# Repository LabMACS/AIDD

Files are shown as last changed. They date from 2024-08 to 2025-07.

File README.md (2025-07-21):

# A.I.D.D.
The Artificial Intelligent Dolphin Deterrent: a novel low-cost intelligent robotic system capable of identifying dolphin vocalizations and consequently responding in real-time to dissuade the dolphins from approaching.

<p float="left">
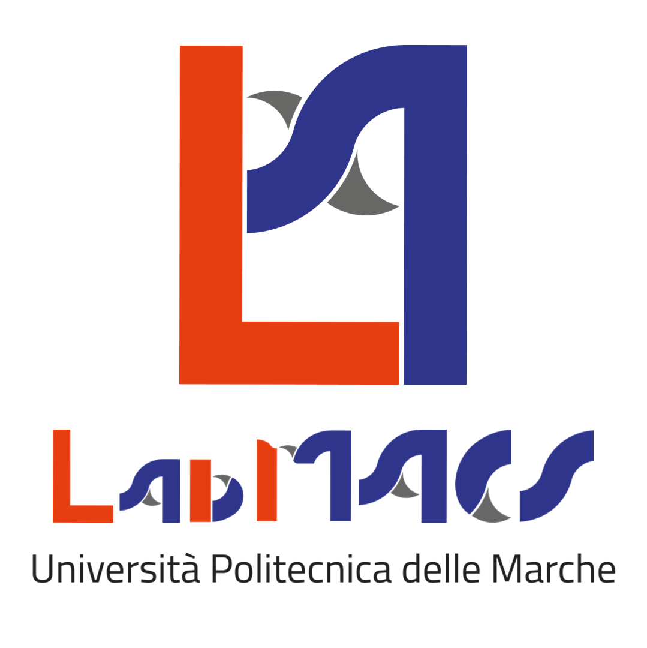
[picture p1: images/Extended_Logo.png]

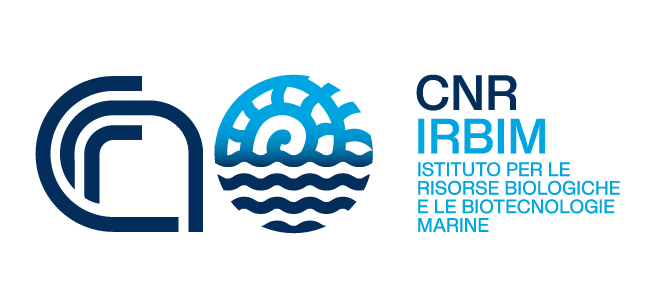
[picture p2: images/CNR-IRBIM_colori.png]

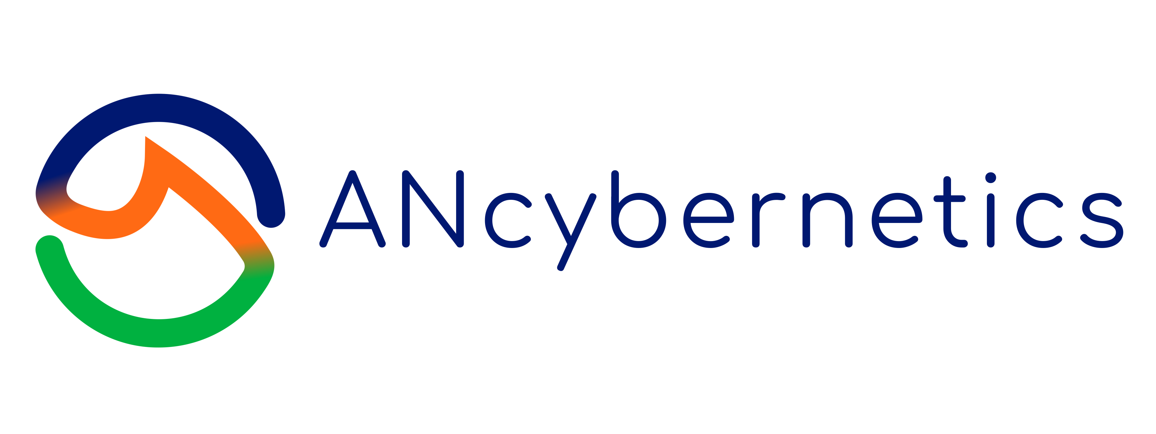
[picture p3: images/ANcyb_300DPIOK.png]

</p>

# Table of contents
1. [Preface](#preface)
2. [Legal](#legal)
    1. [Credits](#credits)
    2. [Funding](#funding) 
    3. [License](#license)

## Preface 
Dolphin bycatch and depredation in commercial fisheries pose serious ecological and socio-economic challenges, often resulting in injury or death of non-target marine mammals and financial loss for fishers. Conventional mitigation strategies, including static acoustic deterrent devices (pingers), have shown limited long-term efficacy due to habituation, non-selective operation, and environmental side effects. In this repository, we introduce the Artificial Intelligent Dolphin Deterrent (A.I.D.D.), a novel low-cost mechatronic system designed to reduce dolphin bycatch through underwater acoustic sensing, real-time machine learning, and programmable deterrent emissions.The device features a hydrophone-based acquisition unit, a Raspberry Pi Zero 2 W for onboard processing, and a dual-function acquisition/emitter system powered by a customized preamplifier and amplifier chain. The computational core of the system is a convolutional neural network (CNN) optimized with TensorFlow Lite to detect dolphin whistles and trigger deterrent sounds only upon verified presence
This repository provides:

    The complete Electronic Scheme of A.I.D.D.

    An advanced version of the convolutional neural network (CNN) optimized with TensorFlow Lite

    The Electronic scheme of the Power Monitoring module and its calculation software

    STL files for 3D printing the hydrophone

A.I.D.D. is a low-cost, fully replicable, and customizable solution that aims to make intelligent bycatch mitigation technologies accessible, representing a promising step toward sustainable and intelligent fishery practices.
  
***
For further information about the project and the A.I.D.D., please look at 
- https://www.irbim.cnr.it/progetto-dettagli/life-delfi/
- Francesco Di Nardo,  Rocco De Marco, Daniele Costa, Alessandro Lucchetti, and David Scaradozzi. A.I.D.D.: A Low-Cost, AI Powered, Acoustic Deterrent to Prevent Dolphin Bycatch and Depredation, Submitted to Science Robotics, July 2025.
- Rocco De Marco, Francesco Di Nardo, Alessandro Rongoni, Laura Screpanti, and David Scaradozzi. Real-Time Dolphin Whistle Detection on Raspberry Pi Zero 2 W with a TFLite Convolutional Neural Network. Robotics 2025, 14, 67. https://doi.org/10.3390/robotics14050067
- David Scaradozzi, Rocco de Marco, Daniel Li Veli, Alessandro Lucchetti, Laura Screpanti, and Francesco Di Nardo, Convolutional Neural Networks for Enhancing Detection of Dolphin Whistles in a Dense Acoustic Environment. IEEE Access, 2024, 12, 127141-127148.  doi: 10.1109/ACCESS.2024.3454815
- Rocco De Marco, Francesco Di Nardo, Alessandro Lucchetti, Massimo Virgili, Andrea Petetta, Daniel Li Veli, Laura Screpanti, Veronica Bartolucci, David Scaradozzi. The Development of a Low-Cost Hydrophone for Passive Acoustic Monitoring of Dolphin’s Vocalizations. Remote Sensing. 2023, 15, 1946. https://doi.org/10.3390/rs15071946
***

## Legal 
### Credits 
If you have any suggestions or comments related to this software, please contact:
* **Project Leader**: [David Scaradozzi](mailto:d.scaradozzi@univpm.it)
* **Project Developer**: [Rocco De Marco](mailto:rocco.demarco@cnr.it)
* **Project Developer**: [Francesco Di Nardo](mailto:f.dinardo@univpm.it)

- *LabMACS, DII, UniversitÃ  Politecnica delle Marche, Via Brecce Bianche, 12, Ancona, 60131, Italy*
- *Institute of Biological Resources and Marine Biotechnology (IRBIM), National Research Council (CNR), Ancona, Italy.*
- *ANcybernetics, Università Politecnica delle Marche, Ancona, Italy.*

[https://www.labmacs.university/](https://www.labmacs.university/)

### Funding  
This work was supported in part by LIFE Financial Instrument of the European Community, Life Delfi Project – Dolphin Experience: Lowering Fishing Interactions (LIFE18NAT/IT/000942) and by the National Recovery and Resilience Plan (NRRP), Mission 4 Component 2 Investment 1.4 (Call for tender No. 3138 of 16 December 2021, rectified by Decree n.3175 of 18 December 2021 of Italian Ministry of University and Research funded by the European Union) NextGenerationEU.

### License 
[][cc-by-nc-sa]

This work is licensed under a
[Creative Commons Attribution-NonCommercial-ShareAlike 4.0 International License][cc-by-nc-sa].

[][cc-by-nc-sa]

[cc-by-nc-sa]: http://creativecommons.org/licenses/by-nc-sa/4.0/
[cc-by-nc-sa-image]: https://licensebuttons.net/l/by-nc-sa/4.0/88x31.png
[cc-by-nc-sa-shield]: https://img.shields.io/badge/License-CC%20BY--NC--SA%204.0-lightgrey.svg

To acknowledge the material, the following information must be reported:
* Attribution: DELFI project
             <[https://www.labmacs.university/](https://www.labmacs.university/)> 
* Title of the Work: AIDD - AI Dolphin Deter 
* Source: [https://github.com/LabMACS/AIDD](https://github.com/LabMACS/AIDD)
* License information: CC BY-NC-SA 4.0

The AIDD - AI Dolphin Deter is free available.

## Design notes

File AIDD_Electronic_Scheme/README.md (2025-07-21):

# A.I.D.D. Electronic schemes
The electronic schemes developed for A.I.D.D.

<p float="left">



</p>

# Table of contents
1. [Preface](#preface)
2. [Legal](#legal)
    1. [Credits](#credits)
    2. [Funding](#funding) 
    3. [License](#license)

## Preface 
This section contains the electronic schemes developed for A.I.D.D.. The "main board" fold includes the schematics, PCB, and Gerber files of the main device, which connects each specialised module composing the A.I.D.D.. This board presents two 40-pins socket connector to mount the Raspberry Pi Zero 2 W and the high-quality audio expansion board, the HiFiBerry DAC+ADC Pro. The board allows to connect the customized preamplifier ("PreAmp THT" fold). The signal preamplifier is composed of Microchip MCP6024 quad operational amplifier, with a constant gain-bandwidth product (10 MHz). It works with a single supply voltage range of 2.5 - 5.5 V. Further pre-assembled modules are pluggeble on the main board, such as the TDA2030A power amp, Step-Up DC-DC Converter, Relay modules and Real-Time Clock module. Further information could be found in the scientific article under submission.

***
For further information about the project, model and parameters, please look at 
- https://www.irbim.cnr.it/progetto-dettagli/life-delfi/
-Francesco Di Nardo, Rocco De Marco, Daniele Costa, Alessandro Lucchetti, and David Scaradozzi. A.I.D.D.: A Low-Cost, AI Powered, Acoustic Deterrent to Prevent Dolphin Bycatch and Depredation, Submitted to Science Robotics, July 2025.
***

## Legal 
### Credits 
If you have any suggestions or comments related to this software, please contact:
* **Project Leader**: [David Scaradozzi](mailto:d.scaradozzi@univpm.it)
* **Project Developer**: [Rocco De Marco](mailto:rocco.demarco@cnr.it)
* **Project Developer**: [Francesco Di Nardo](mailto:f.dinardo@univpm.it)

- *LabMACS, DII, UniversitÃ  Politecnica delle Marche, Via Brecce Bianche, 12, Ancona, 60131, Italy*
- *Institute of Biological Resources and Marine Biotechnology (IRBIM), National Research Council (CNR), Ancona, Italy.*
- *ANcybernetics, Università Politecnica delle Marche, Ancona, Italy.*

[https://www.labmacs.university/](https://www.labmacs.university/)

### Funding  
This work was supported in part by LIFE Financial Instrument of the European Community, Life Delfi Project – Dolphin Experience: Lowering Fishing Interactions (LIFE18NAT/IT/000942) and by the National Recovery and Resilience Plan (NRRP), Mission 4 Component 2 Investment 1.4 (Call for tender No. 3138 of 16 December 2021, rectified by Decree n.3175 of 18 December 2021 of Italian Ministry of University and Research funded by the European Union) NextGenerationEU.

### License 
[][cc-by-nc-sa]

This work is licensed under a
[Creative Commons Attribution-NonCommercial-ShareAlike 4.0 International License][cc-by-nc-sa].

[][cc-by-nc-sa]

[cc-by-nc-sa]: http://creativecommons.org/licenses/by-nc-sa/4.0/
[cc-by-nc-sa-image]: https://licensebuttons.net/l/by-nc-sa/4.0/88x31.png
[cc-by-nc-sa-shield]: https://img.shields.io/badge/License-CC%20BY--NC--SA%204.0-lightgrey.svg

To acknowledge the material, the following information must be reported:
* Attribution: DELFI project
             <[https://www.labmacs.university/](https://www.labmacs.university/)> 
* Title of the Work: AIDD - AI Dolphin Deter 
* Source: [https://github.com/LabMACS/AIDD](https://github.com/LabMACS/AIDD)
* License information: CC BY-NC-SA 4.0

The AIDD - AI Dolphin Deter is free available.

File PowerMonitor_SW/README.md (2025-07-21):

# Monitoring of Power Consumption
Software for the monitoring of A.I.D.D. power consumption.

<p float="left">



</p>

# Table of contents
1. [Preface](#preface)
2. [Legal](#legal)
    1. [Credits](#credits)
    2. [Funding](#funding) 
    3. [License](#license)

## Preface 
The enclosed routine (INA_219_Logger) is designed to provide an estimation of the power consumption of the A.I.D.D. device using a 12-bit I2C output digital power monitor, the INA219 sensor. The sensor was connected to a monitoring system based on a Raspberry Pi 3 Model A running Python sampling software. This setup acquires the voltage and current supplied to the A.I.D.D. system and classifies seven different operating stages: 

1.	Data read from audio device 
2.	STFT process
3.	Image conversion (Plot)
4.	CNN inference
5.	Data logging (in case of positive events)
6.	Sleep mode (waiting for the timestep of 0.4s)
7.	Start-up of the environment

The running states were transmitted from the Raspberry Pi Zero 2 W of the device to the monitoring Raspberry Pi 3 Model A via a three-wire GPIO connection (using GPIO pins 27, 17, and 22). These pins encoded the current running stage as a 3-bit integer value. The trials were conducted using the same criteria as in the previous section (Real-time software validation). 

***
For further information about the project, model and parameters, please look at 
- https://www.irbim.cnr.it/progetto-dettagli/life-delfi/
- Francesco Di Nardo, David Scaradozzi, Rocco De Marco, Laura Screpanti, and Alessandro Lucchetti, Intelligent identification of dolphin whistle in acoustic signals via convolutional neural networks, Science Advances, Submitted
***

## Legal 
### Credits 
If you have any suggestions or comments related to this software, please contact:
* **Project Leader**: [David Scaradozzi](mailto:d.scaradozzi@univpm.it)
* **Project Developer**: [Rocco De Marco](mailto:rocco.demarco@cnr.it)
* **Project Developer**: [Francesco Di Nardo](mailto:f.dinardo@univpm.it)

- *LabMACS, DII, UniversitÃ  Politecnica delle Marche, Via Brecce Bianche, 12, Ancona, 60131, Italy*
- *Institute of Biological Resources and Marine Biotechnology (IRBIM), National Research Council (CNR), Ancona, Italy.*
- *ANcybernetics, Università Politecnica delle Marche, Ancona, Italy.*

[https://www.labmacs.university/](https://www.labmacs.university/)

### Funding  
This work was supported in part by LIFE Financial Instrument of the European Community, Life Delfi Project – Dolphin Experience: Lowering Fishing Interactions (LIFE18NAT/IT/000942) and by the National Recovery and Resilience Plan (NRRP), Mission 4 Component 2 Investment 1.4 (Call for tender No. 3138 of 16 December 2021, rectified by Decree n.3175 of 18 December 2021 of Italian Ministry of University and Research funded by the European Union) NextGenerationEU.

### License 
[][cc-by-nc-sa]

This work is licensed under a
[Creative Commons Attribution-NonCommercial-ShareAlike 4.0 International License][cc-by-nc-sa].

[][cc-by-nc-sa]

[cc-by-nc-sa]: http://creativecommons.org/licenses/by-nc-sa/4.0/
[cc-by-nc-sa-image]: https://licensebuttons.net/l/by-nc-sa/4.0/88x31.png
[cc-by-nc-sa-shield]: https://img.shields.io/badge/License-CC%20BY--NC--SA%204.0-lightgrey.svg

To acknowledge the material, the following information must be reported:
* Attribution: DELFI project
             <[https://www.labmacs.university/](https://www.labmacs.university/)> 
* Title of the Work: AIDD - AI Dolphin Deter 
* Source: [https://github.com/LabMACS/AIDD](https://github.com/LabMACS/AIDD)
* License information: CC BY-NC-SA 4.0

The AIDD - AI Dolphin Deter is free available.

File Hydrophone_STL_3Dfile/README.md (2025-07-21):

# Hydrophone STL 3Dfile
The model files for 3D print of self-made CoPiDi hydrophone

<p float="left">



</p>

# Table of contents
1. [Preface](#preface)
2. [Legal](#legal)
    1. [Credits](#credits)
    2. [Funding](#funding) 
    3. [License](#license)

## Preface 
This section shares the STL files for the specific-developed enclosure cap that embeds the hydrophone/emitter device, based on piezo caps. This cap is designed to hermetically seal a 40cm-long Teflon tube that contains the device hardware in order to ensure watertightness. This component was made using an industrial-quality SLA (stereolithography) 3D printer, reproducing the already validated CoPiDi* hydrophone, with same form and dimensions. The cap can be removed to access the hydrophone and other components without compromising the waterproofing.  
***

Further details about CoPiDi hydrophone could be found in "De Marco, R.; Di Nardo, F.; Lucchetti, A.; Virgili, M.; Petetta, A.; Li Veli, D.; Screpanti, L.; Rocco De Marco, Francesco Di Nardo, Alessandro Lucchetti, Massimo Virgili, Andrea Petetta, Daniel Li Veli, Laura Screpanti, Veronica Bartolucci, David Scaradozzi. The Development of a Low-Cost Hydrophone for Passive Acoustic Monitoring of Dolphin’s Vocalizations. Remote Sensing. 2023, 15, 1946. https://doi.org/10.3390/rs15071946

For further information about the project, model and parameters, please look at 
- https://www.irbim.cnr.it/progetto-dettagli/life-delfi/
***

## Legal 
### Credits 
If you have any suggestions or comments related to this software, please contact:
* **Project Leader**: [David Scaradozzi](mailto:d.scaradozzi@univpm.it)
* **Project Developer**: [Rocco De Marco](mailto:rocco.demarco@cnr.it)
* **Project Developer**: [Francesco Di Nardo](mailto:f.dinardo@univpm.it)

- *LabMACS, DII, UniversitÃ  Politecnica delle Marche, Via Brecce Bianche, 12, Ancona, 60131, Italy*
- *Institute of Biological Resources and Marine Biotechnology (IRBIM), National Research Council (CNR), Ancona, Italy.*
- *ANcybernetics, Università Politecnica delle Marche, Ancona, Italy.*

[https://www.labmacs.university/](https://www.labmacs.university/)

### Funding  
This work was supported in part by LIFE Financial Instrument of the European Community, Life Delfi Project – Dolphin Experience: Lowering Fishing Interactions (LIFE18NAT/IT/000942) and by the National Recovery and Resilience Plan (NRRP), Mission 4 Component 2 Investment 1.4 (Call for tender No. 3138 of 16 December 2021, rectified by Decree n.3175 of 18 December 2021 of Italian Ministry of University and Research funded by the European Union) NextGenerationEU.

### License 
[][cc-by-nc-sa]

This work is licensed under a
[Creative Commons Attribution-NonCommercial-ShareAlike 4.0 International License][cc-by-nc-sa].

[][cc-by-nc-sa]

[cc-by-nc-sa]: http://creativecommons.org/licenses/by-nc-sa/4.0/
[cc-by-nc-sa-image]: https://licensebuttons.net/l/by-nc-sa/4.0/88x31.png
[cc-by-nc-sa-shield]: https://img.shields.io/badge/License-CC%20BY--NC--SA%204.0-lightgrey.svg

To acknowledge the material, the following information must be reported:
* Attribution: DELFI project
             <[https://www.labmacs.university/](https://www.labmacs.university/)> 
* Title of the Work: AIDD - AI Dolphin Deter 
* Source: [https://github.com/LabMACS/AIDD](https://github.com/LabMACS/AIDD)
* License information: CC BY-NC-SA 4.0

The AIDD - AI Dolphin Deter is free available.

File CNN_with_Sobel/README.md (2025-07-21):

# CNN trained with Sobel-filtered spectrograms
This section of the A.I.D.D. repository introduces the basic algorithm to test the functionality of the CNN model trained to recognize bottlenose dolphin whistles.

<p float="left">



</p>

# Table of contents
1. [Preface](#preface)
2. [Installation](#installation)
    1. [Requirements](#requirements)
    2. [Usage](#run)
3. [Legal](#legal)
    1. [Credits](#credits)
    2. [Funding](#funding) 
    3. [License](#license)

## Preface 
This section of the A.I.D.D. repository provides the convolutional neural network (CNN) that forms the computational core of the device, designed to identify dolphin whistles from spectrograms extracted from underwater audio recordings. Prior to CNN processing, spectrograms undergo a vertical Sobel filter that enhances the whistle waveform, improving both CNN training and detection performance. Two distinct datasets of dolphin vocalizations were used to evaluate CNN performance, with results showing that, in the best-case scenario, nearly all whistles were correctly identified (99.8%), and the mean model accuracy, precision, recall, and F1-score never dropped below 99.0%. Model effectiveness remained high even under challenging conditions with overlapping noise or other vocalizations. Moreover, the computation speed is fully compatible with real-time applications. The robustness of this model across environments and its low computational demand make this approach highly suitable for intelligent robotic solutions aimed at monitoring and mitigating underwater interactions.

The neural network presented here is an evolution of the one introduced in:

D. Scaradozzi, R. de Marco, D. Li Veli, A. Lucchetti, L. Screpanti, and F. Di Nardo, 'Convolutional Neural Networks for Enhancing Detection of Dolphin Whistles in a Dense Acoustic Environment,' in IEEE Access, vol. 12, pp. 127141-127148, 2024, doi: 10.1109/ACCESS.2024.3454815

which was originally used as the computational core of the device

***
For further information about the project, model and parameters, please look at 
- https://www.irbim.cnr.it/progetto-dettagli/life-delfi/
-  David Scaradozzi, Rocco De Marco, Laura Screpanti, and Francesco Di Nardo, Intelligent Identification of Dolphin Whistle in Acoustic Signals via Deep Learning, Scientific Reports, Submitted
***

## Installation 
### Requirements 
* TbD 
  
### Usage 
This simple application requires that spectrograms be prepared by applying a Sobel vertical filter and saved in PNG format with a resolution of 300x150 pixels. Files containing whistles should have filenames starting with POS, otherwise NEG. All these files should be saved in a folder named "sobel". Please note: a sample trained model is available in "Release"

## Legal 
### Credits 
If you have any suggestions or comments related to this software, please contact:
* **Project Leader**: [David Scaradozzi](mailto:d.scaradozzi@univpm.it)
* **Project Developer**: [Rocco De Marco](mailto:rocco.demarco@cnr.it)
* **Project Developer**: [Francesco Di Nardo](mailto:f.dinardo@univpm.it)

- *LabMACS, DII, UniversitÃ  Politecnica delle Marche, Via Brecce Bianche, 12, Ancona, 60131, Italy*
- *Institute of Biological Resources and Marine Biotechnology (IRBIM), National Research Council (CNR), Ancona, Italy.*
- *ANcybernetics, Università Politecnica delle Marche, Ancona, Italy.*

[https://www.labmacs.university/](https://www.labmacs.university/)

### Funding  
This work was supported in part by LIFE Financial Instrument of the European Community, Life Delfi Project – Dolphin Experience: Lowering Fishing Interactions (LIFE18NAT/IT/000942) and by the National Recovery and Resilience Plan (NRRP), Mission 4 Component 2 Investment 1.4 (Call for tender No. 3138 of 16 December 2021, rectified by Decree n.3175 of 18 December 2021 of Italian Ministry of University and Research funded by the European Union) NextGenerationEU.

### License 
[][cc-by-nc-sa]

This work is licensed under a
[Creative Commons Attribution-NonCommercial-ShareAlike 4.0 International License][cc-by-nc-sa].

[][cc-by-nc-sa]

[cc-by-nc-sa]: http://creativecommons.org/licenses/by-nc-sa/4.0/
[cc-by-nc-sa-image]: https://licensebuttons.net/l/by-nc-sa/4.0/88x31.png
[cc-by-nc-sa-shield]: https://img.shields.io/badge/License-CC%20BY--NC--SA%204.0-lightgrey.svg

To acknowledge the material, the following information must be reported:
* Attribution: DELFI project
             <[https://www.labmacs.university/](https://www.labmacs.university/)> 
* Title of the Work: AIDD - AI Dolphin Deter 
* Source: [https://github.com/LabMACS/AIDD](https://github.com/LabMACS/AIDD)
* License information: CC BY-NC-SA 4.0

The AIDD - AI Dolphin Deter is free available.

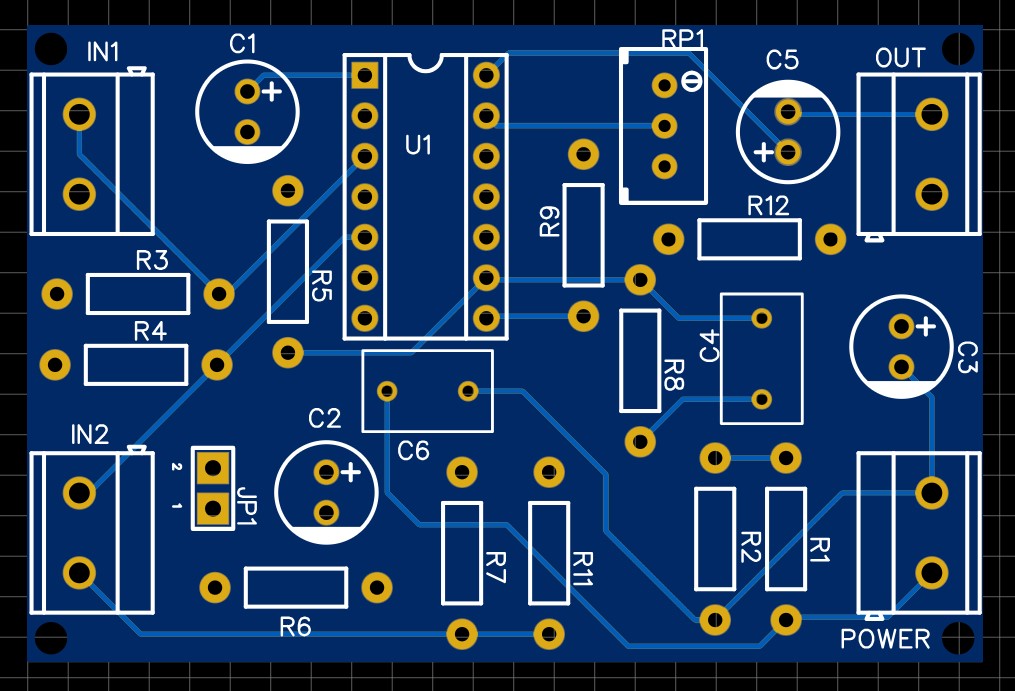
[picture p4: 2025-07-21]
AIDD_Electronic_Scheme/PreAmp THT/PCB_PreAmp_THT_2Dview_TOP.jpg

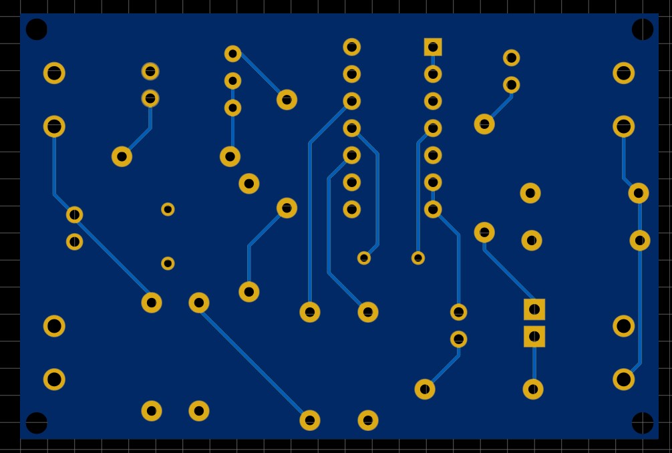
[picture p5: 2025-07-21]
AIDD_Electronic_Scheme/PreAmp THT/PCB_PreAmp_THT_2Dview_BOTTOM.jpg

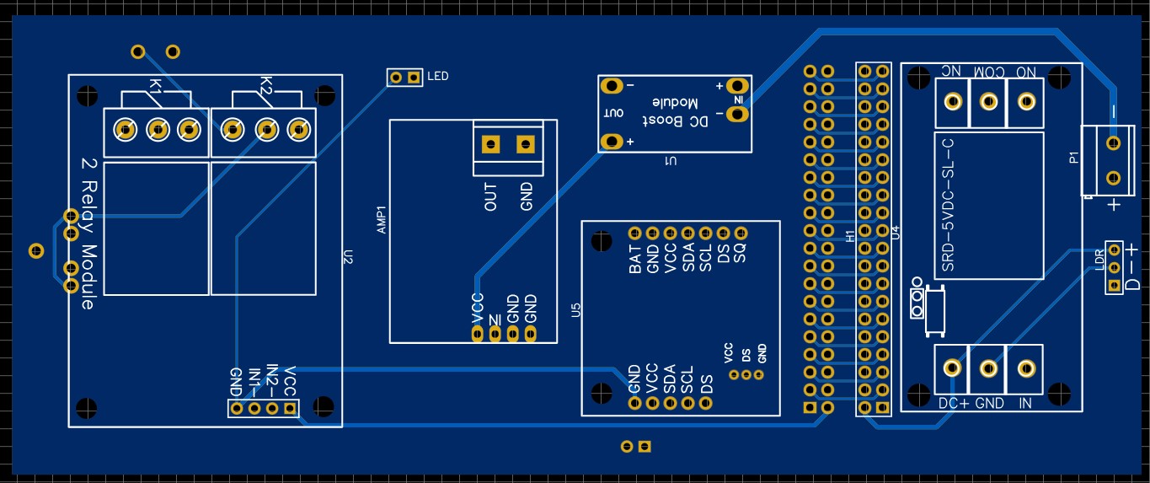
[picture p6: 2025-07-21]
AIDD_Electronic_Scheme/Main Board/PCB_V7.5_2DView_BOTTOM.jpg

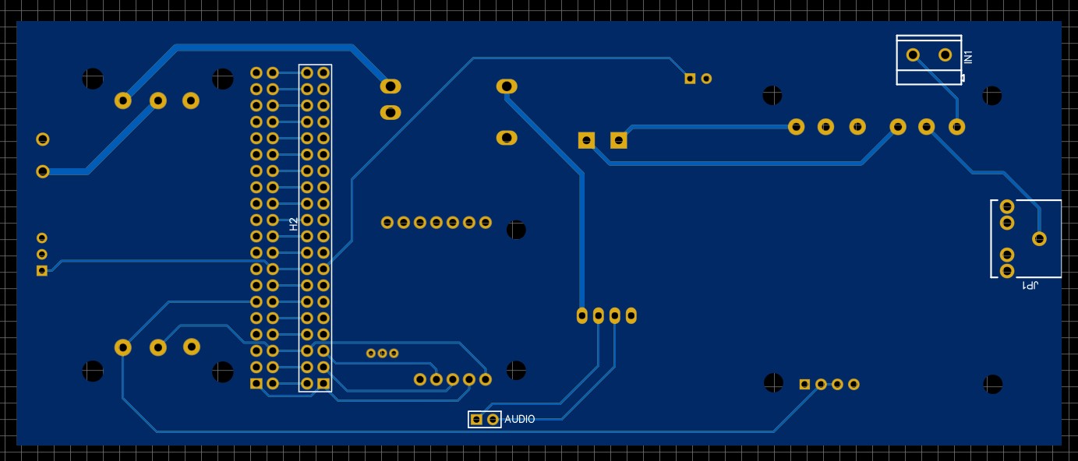
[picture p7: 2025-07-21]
AIDD_Electronic_Scheme/Main Board/PCB_V7.5_2Dview_TOP.jpg

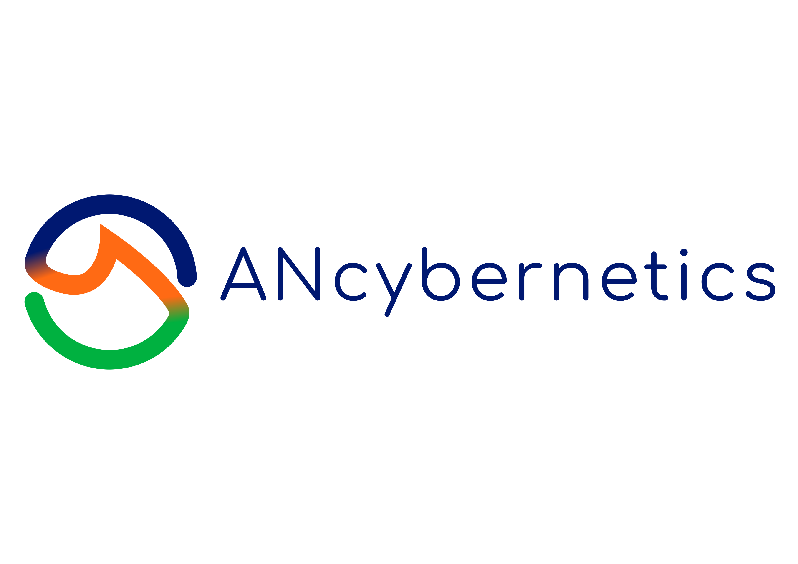
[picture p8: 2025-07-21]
images/ANcyb_300DPI.png

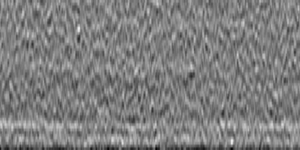
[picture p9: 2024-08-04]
CNN_with_Sobel/sobel/NEG_20211120_102109_192_0502.png

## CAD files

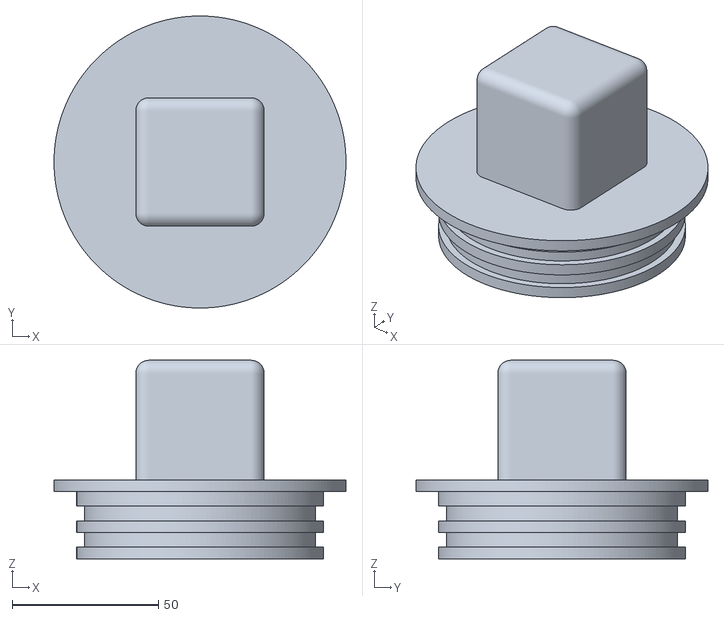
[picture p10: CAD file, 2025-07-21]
Hydrophone_STL_3Dfile/Tappo Mike Inox.stl
100.0 x 100.0 x 68.0

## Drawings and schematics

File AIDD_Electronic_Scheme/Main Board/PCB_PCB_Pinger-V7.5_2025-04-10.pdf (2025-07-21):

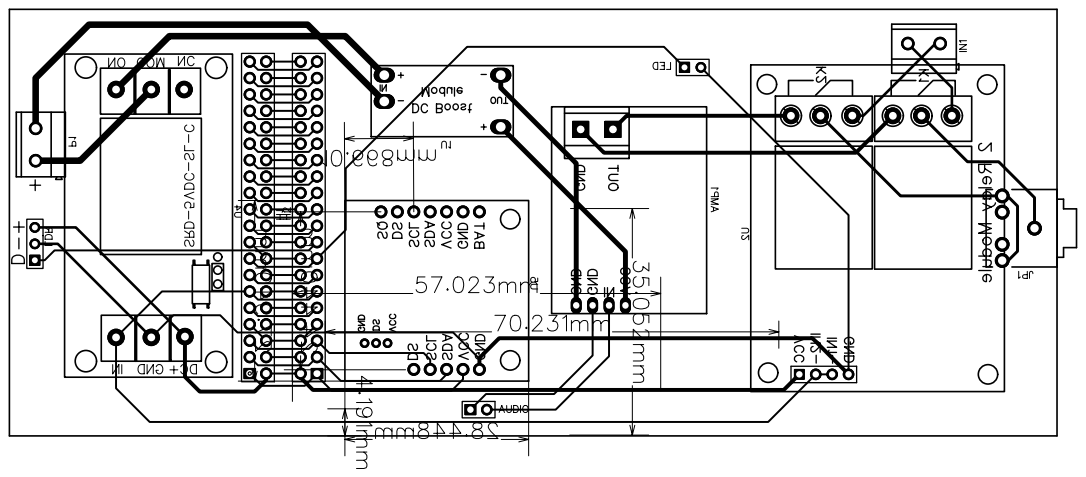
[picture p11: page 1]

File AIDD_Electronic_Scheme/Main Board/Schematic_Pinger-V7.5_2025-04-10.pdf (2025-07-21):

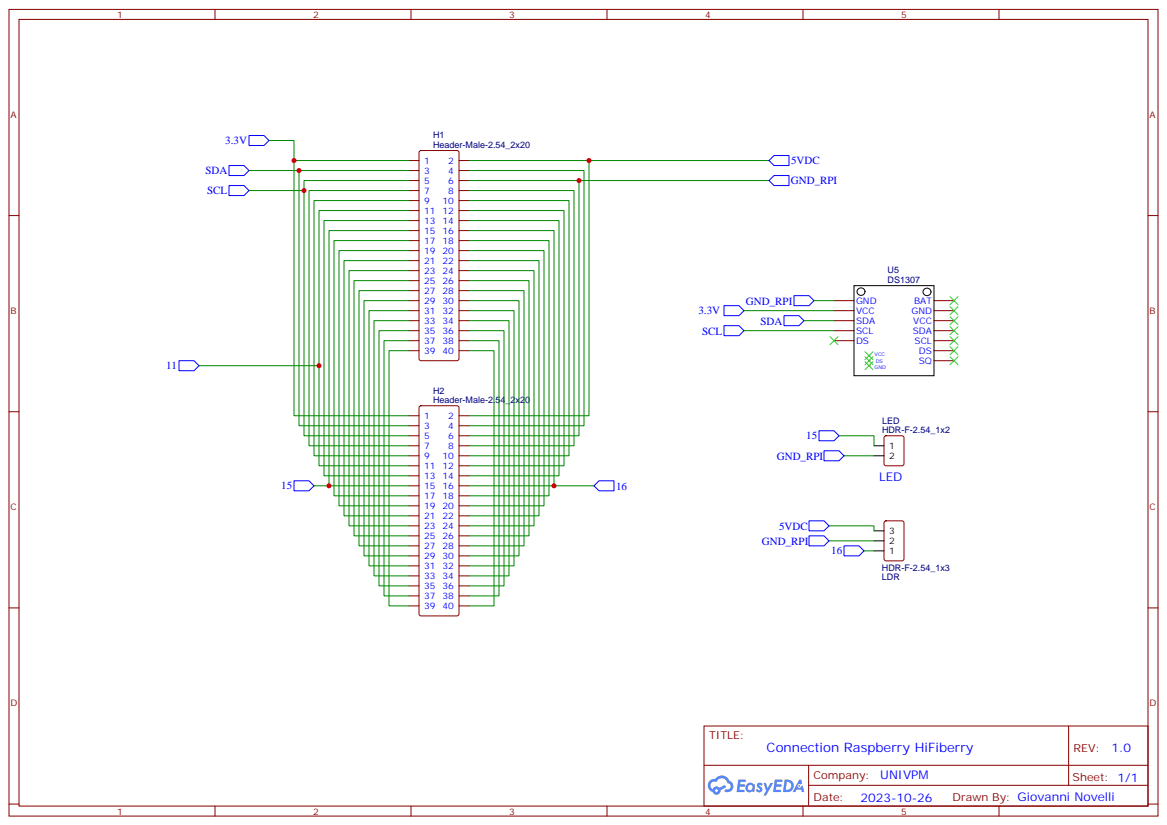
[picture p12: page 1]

Drawn By: Giovanni Novelli

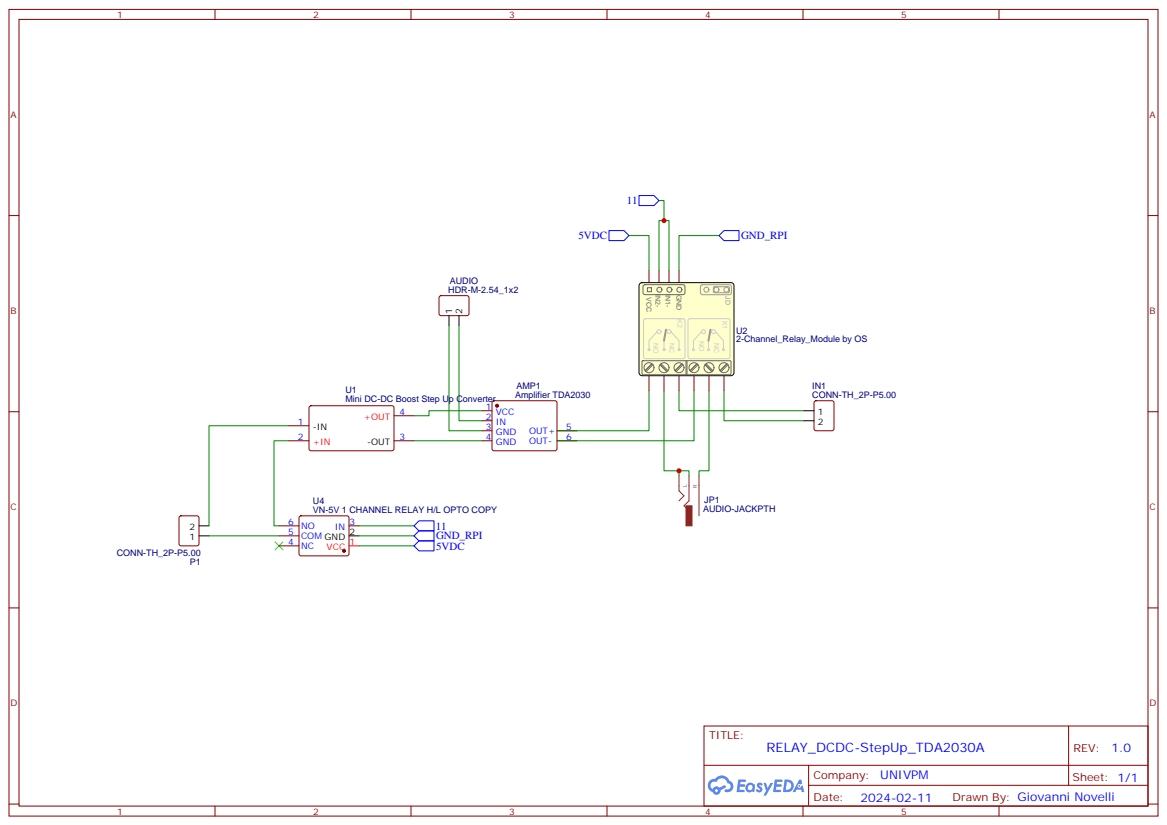
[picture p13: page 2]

Mini DC-DC Boost Step Up Converter
+OUT 4

Drawn By: Giovanni Novelli

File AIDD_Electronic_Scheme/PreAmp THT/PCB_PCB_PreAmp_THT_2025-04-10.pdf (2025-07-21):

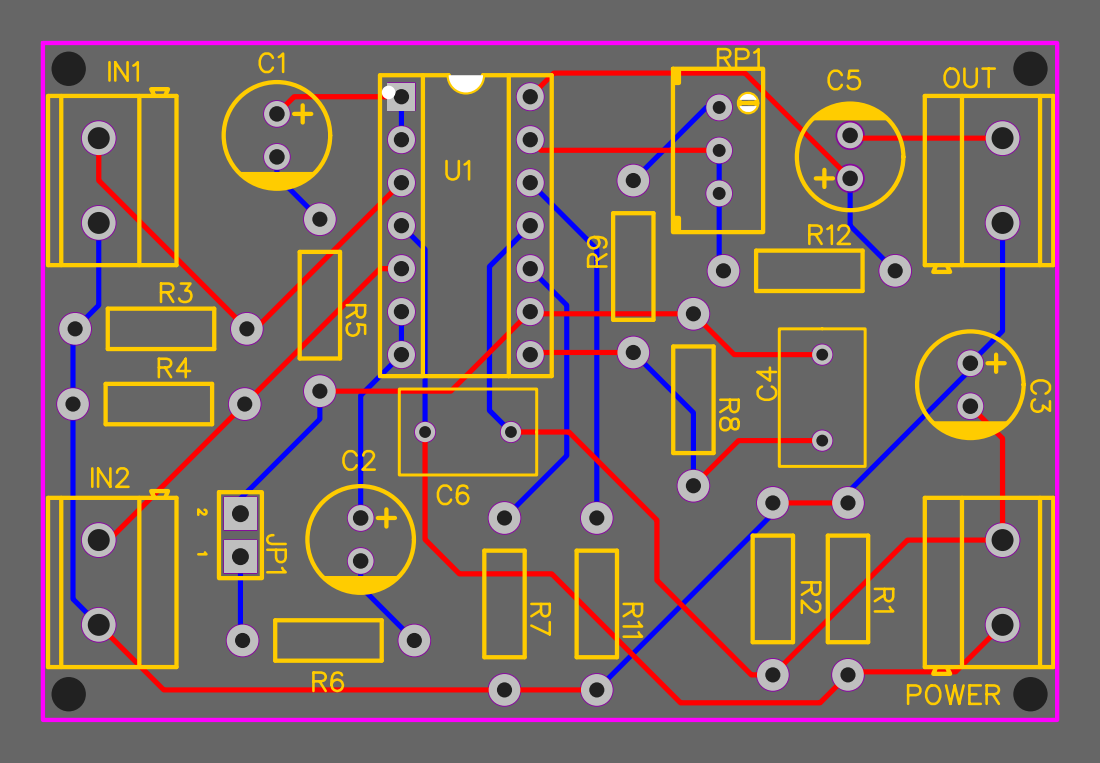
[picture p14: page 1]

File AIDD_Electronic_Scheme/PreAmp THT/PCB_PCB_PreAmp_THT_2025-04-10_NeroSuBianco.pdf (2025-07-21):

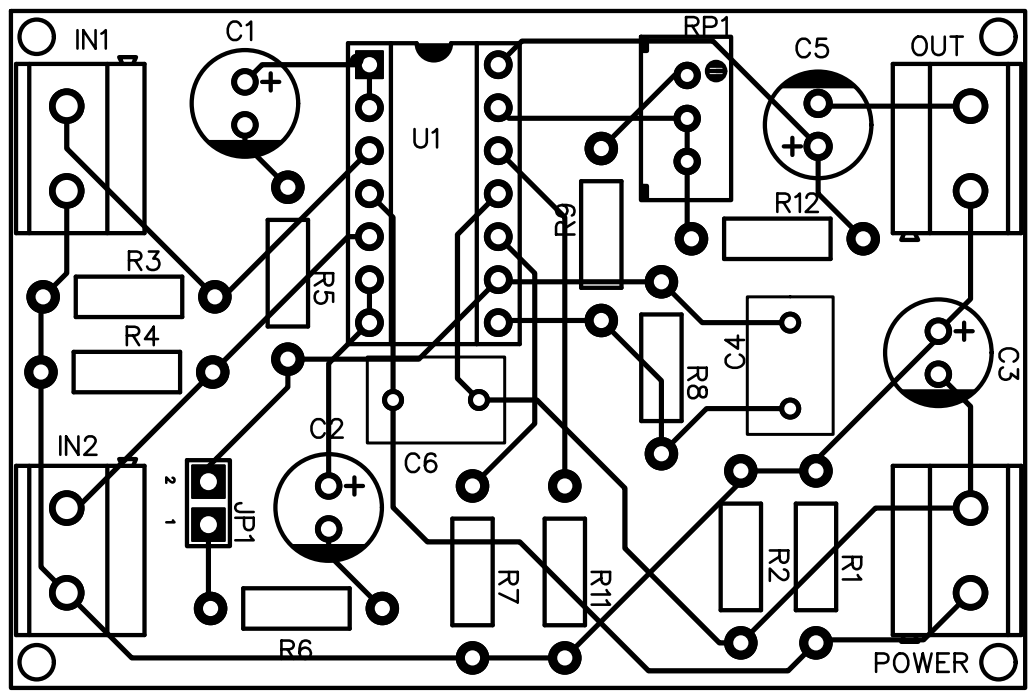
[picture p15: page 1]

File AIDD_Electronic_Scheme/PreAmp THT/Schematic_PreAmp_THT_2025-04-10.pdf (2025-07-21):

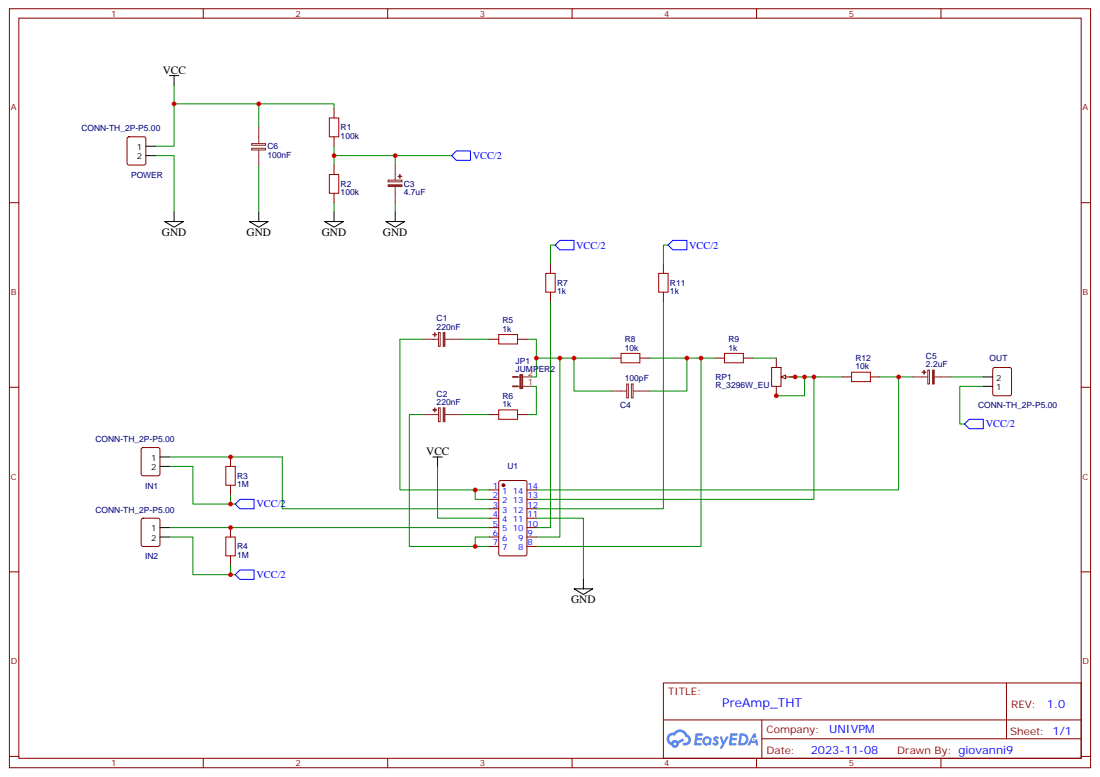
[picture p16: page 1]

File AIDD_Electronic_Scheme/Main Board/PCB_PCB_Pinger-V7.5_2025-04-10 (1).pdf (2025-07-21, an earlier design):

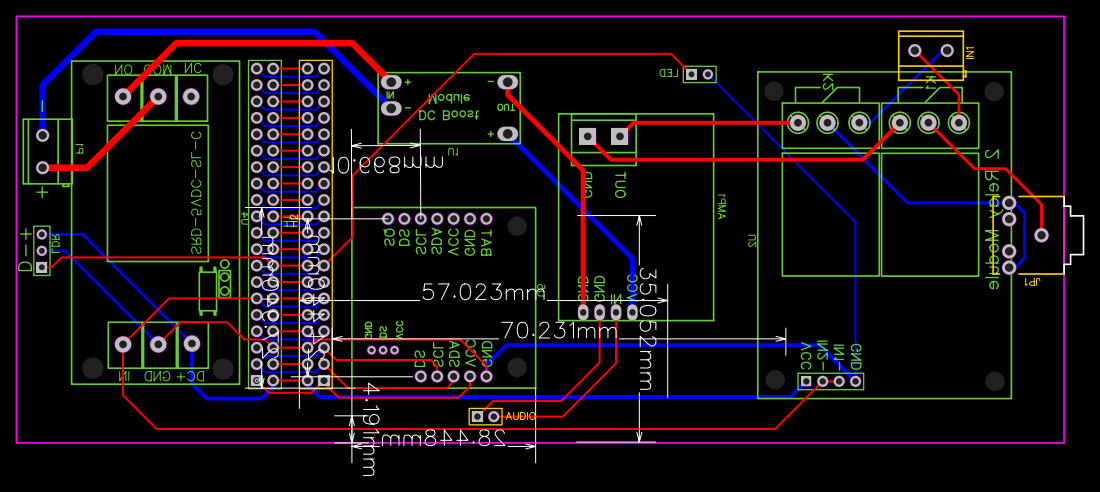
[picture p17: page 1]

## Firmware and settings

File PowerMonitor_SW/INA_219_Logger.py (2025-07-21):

import csv
import time
import smbus
import RPi.GPIO as GPIO

# GPIO Configuration for computatinal stage
GPIO.setmode(GPIO.BCM)
GPIO.setup(17, GPIO.IN)
GPIO.setup(27, GPIO.IN)
GPIO.setup(22, GPIO.IN)

def read_state():
    return (GPIO.input(22) << 2) | (GPIO.input(27) << 1) | GPIO.input(17)

# INA219 Configuration
bus = smbus.SMBus(1)
INA219_ADDRESS = 0x40
INA219_REG_CONFIG = 0x00
INA219_REG_SHUNT_VOLTAGE = 0x01
INA219_REG_BUS_VOLTAGE = 0x02
INA219_REG_CALIBRATION = 0x05

CONFIG_10KSPS = (
    (0 << 13) |  # BRNG=16V
    (2 << 11) |  # PG=±160mV 
    (3 << 7)  |  # BADC=12bit
    (3 << 3)  |  # SADC=12bit
    7            # MODE=continuous
)

def write_reg(reg, value):
    bus.write_word_data(INA219_ADDRESS, reg, ((value >> 8) & 0xFF) | ((value & 0xFF) << 8))

def read_reg(reg):
    value = bus.read_word_data(INA219_ADDRESS, reg)
    return ((value << 8) & 0xFF00) | (value >> 8)

# INA219 Init
write_reg(INA219_REG_CONFIG, CONFIG_10KSPS)
write_reg(INA219_REG_CALIBRATION, 4096)

def read_raw_voltages():
    shunt_raw = read_reg(INA219_REG_SHUNT_VOLTAGE)
    bus_raw = read_reg(INA219_REG_BUS_VOLTAGE)
    return bus_raw & 0xFFFF, shunt_raw

def main():
    start_time = time.time()
    sample_count = 0
    interval_start_time = start_time
    interval_sample_count = 0
    interval_v_sum = 0
    interval_a_sum = 0
    interval_w_sum = 0

    with open('power_data.csv', mode='w', newline='') as file:
        writer = csv.writer(file)
        writer.writerow(['timestamp', 'V', 'A', 'W', 'Exec_Stage'])

        while True:
            try:
                bus_raw, shunt_raw = read_raw_voltages()
                timestamp = time.time() - start_time
                state = read_state()

                if shunt_raw >= 32768:
                    shunt_raw -= 65536

                v_bus = (bus_raw >> 3) * 0.004
                v_shunt = shunt_raw * 0.00001
                current = v_shunt / 0.1
                watt = current * v_bus

                writer.writerow([f"{timestamp:.8f}", f"{v_bus:.3f}", f"{current:.4f}", f"{watt:.4f}", state])

                sample_count += 1
                interval_sample_count += 1
                interval_v_sum += v_bus
                interval_a_sum += current
                interval_w_sum += watt

                # Statisctics summary (every 5 seconds)
                if time.time() - interval_start_time >= 5:
                    interval_duration = time.time() - interval_start_time
                    avg_sample_rate = interval_sample_count / interval_duration
                    avg_v = interval_v_sum / interval_sample_count
                    avg_a = interval_a_sum / interval_sample_count
                    avg_w = interval_w_sum / interval_sample_count

                    print(f"\n[STATISTICS - Last 5s]")
                    print(f"Samples: {sample_count} (in interval: {interval_sample_count})")
                    print(f"Mean frequancy: {avg_sample_rate:.2f} Hz")
                    print(f"Mean V: {avg_v:.3f} V, Mean A: {avg_a:.4f} A, Mean W: {avg_w:.4f} W\n")

                    # Reset 
                    interval_start_time = time.time()
                    interval_sample_count = 0
                    interval_v_sum = 0
                    interval_a_sum = 0
                    interval_w_sum = 0

                    if sample_count > 220000:
                       exit()

            except Exception as e:
                print("Error:", e)
                time.sleep(1)

if __name__ == "__main__":
    main()
